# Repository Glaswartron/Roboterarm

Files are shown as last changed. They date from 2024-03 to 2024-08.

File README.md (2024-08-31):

DIY Roboterarm mit 3 Freiheitsgraden und Controller, der Servos und einen Stepper-Motor verwendet und komplett mit Fusion 360 und dem 3D-Drucker konstruiert wurde.

Der gesamte Arm kann am Fuß rotiert werden, hierfür ist ein Stepper-Motor mit einem simplem Getriebe zuständig, der im Fuß verbaut ist.  
Der Arm besteht aus einer unteren Halterung, die den unteren Servo aufnimmt. Dieser bewegt den gesamten Arm.  
Am Arm selber ist ein zweites Gelenk, das heißt ein zweiter Servo, verbaut, der den oberen Teil des Arms bewegt.  
Alle drei Motoren werden von einem Arduino mithilfe eines Joystick-Controllers gesteuert.  

Beim Bau und Test gab es einige Herausforderungen:
- Das größte Problem ist ein mechanisches: Die Servos können den Arm zwar bewegen, allerdings reicht ihr Drehmoment bzw. ihr Getriebe nicht ganz aus, 
um den Arm z.B. im "ausgestreckten" Zustand zu halten. Um dies zu lösen habe ich den Arm etwas verkürzt, 
versucht beim 3D-Druck Gewicht zu sparen und insbesondere Gummibänder mit Halterungen verbaut, die der Gewichtskraft ein zusätzlich Gegendrehmoment entgegensetzen.
Das funktioniert leider noch nicht perfekt, aber gut genug. Eine mögliche Weiterentwicklung wären stärkere Servos.
- Der Stepper-Motor benötigt einen Treiber mit eigener Stromversorgung und Kühlkörper (läuft heiß). Hierfür kann eine 9V-Batterie angeschlossen werden. Als rudimentäre
Spannungsstabilisierung zwischen Batterie und Stepper-Treiber dient ein (Elektrolyt)Kondensator. Eine mögliche Weiterentwicklung wäre eine bessere Spannungsversorgung mit Spannungsregler(n),
die dann auch gleich den Arduino mitspeisen kann.

Bilder aus der Entwicklung:

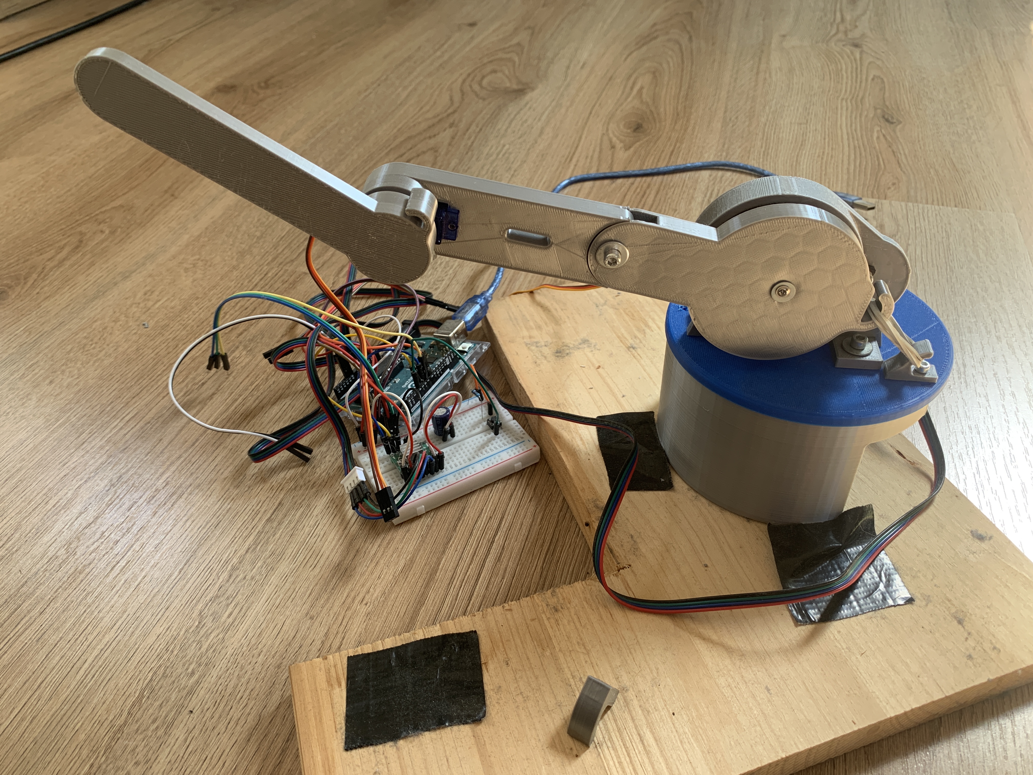
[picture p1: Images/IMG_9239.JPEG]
Vorderansicht

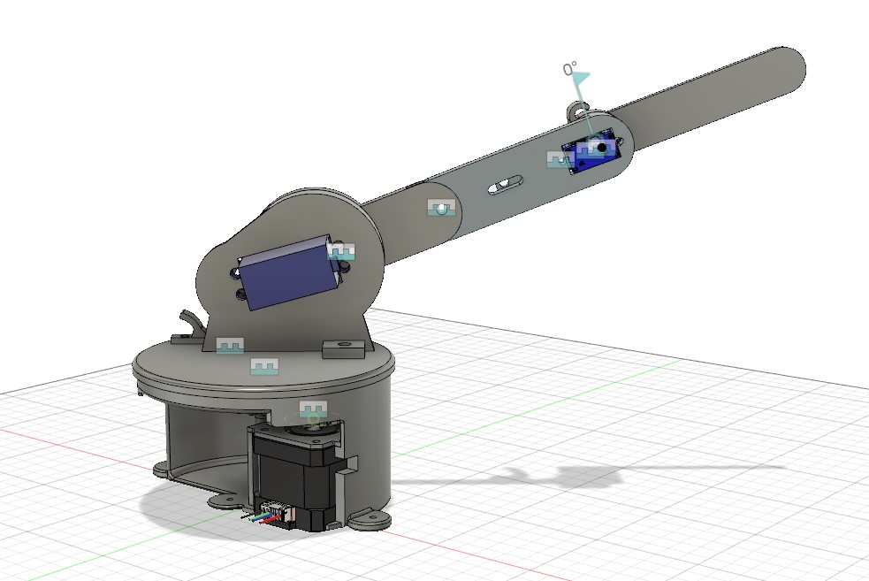
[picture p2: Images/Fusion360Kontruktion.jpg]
Fusion 360 Screenshot

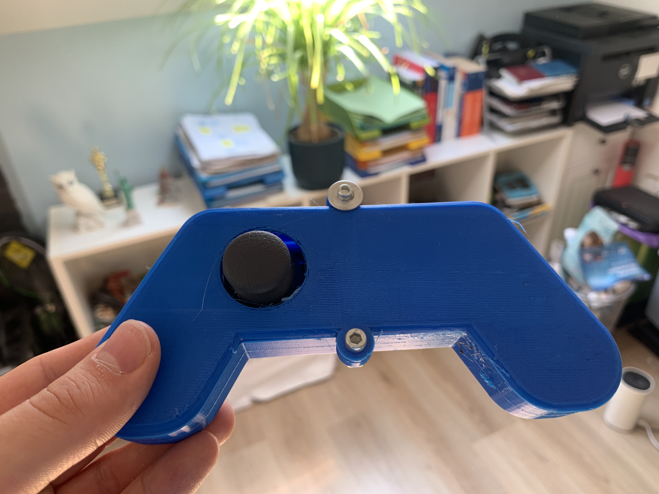
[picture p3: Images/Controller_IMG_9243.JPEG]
Controller

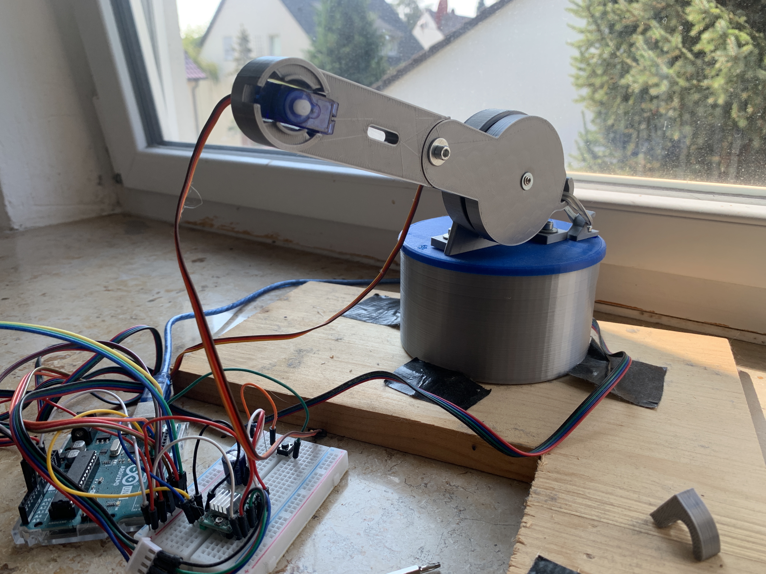
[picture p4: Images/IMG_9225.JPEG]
Vorderansicht Unterarm

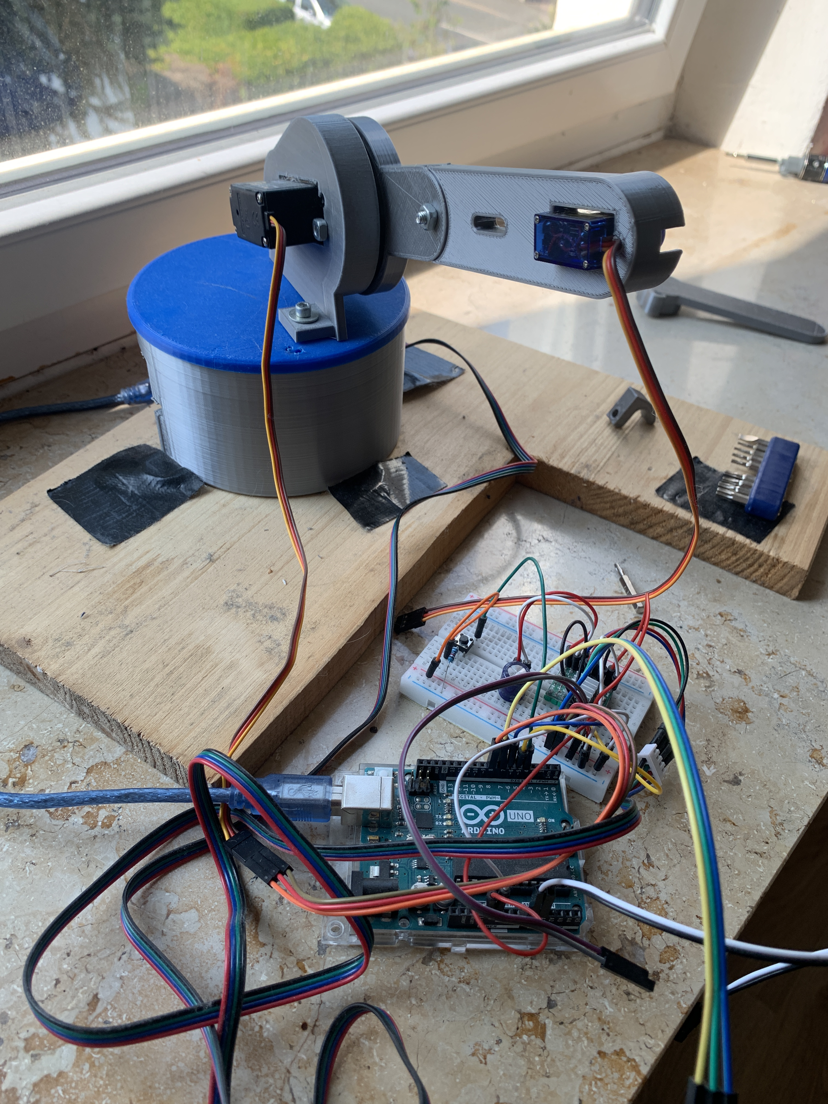
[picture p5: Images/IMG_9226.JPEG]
Vorderansicht Unterarm Seite

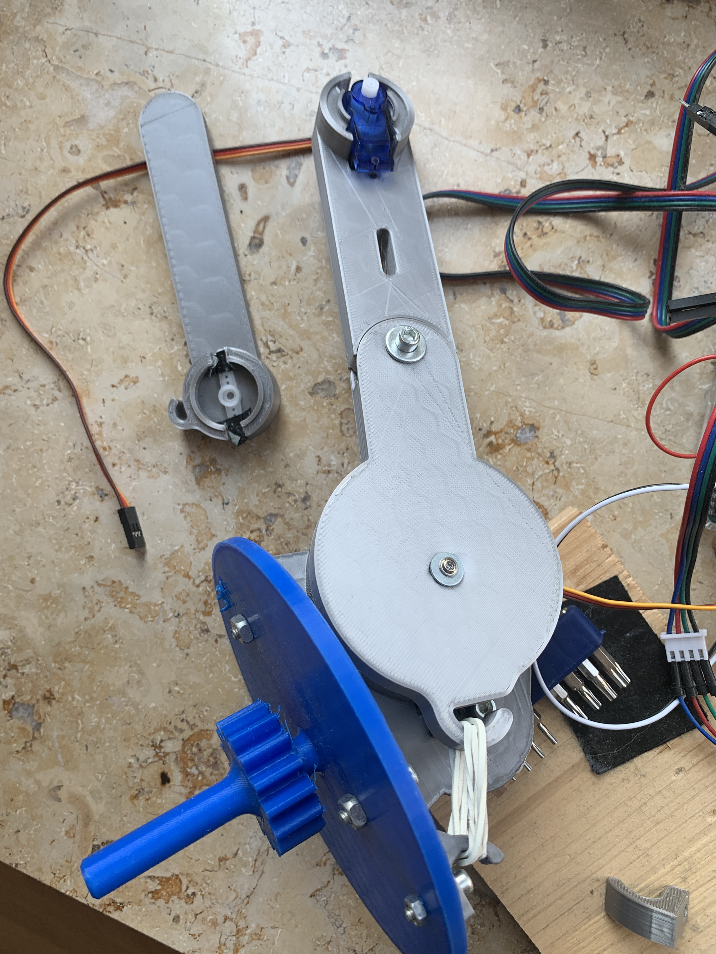
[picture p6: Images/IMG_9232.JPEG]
Einzelteile

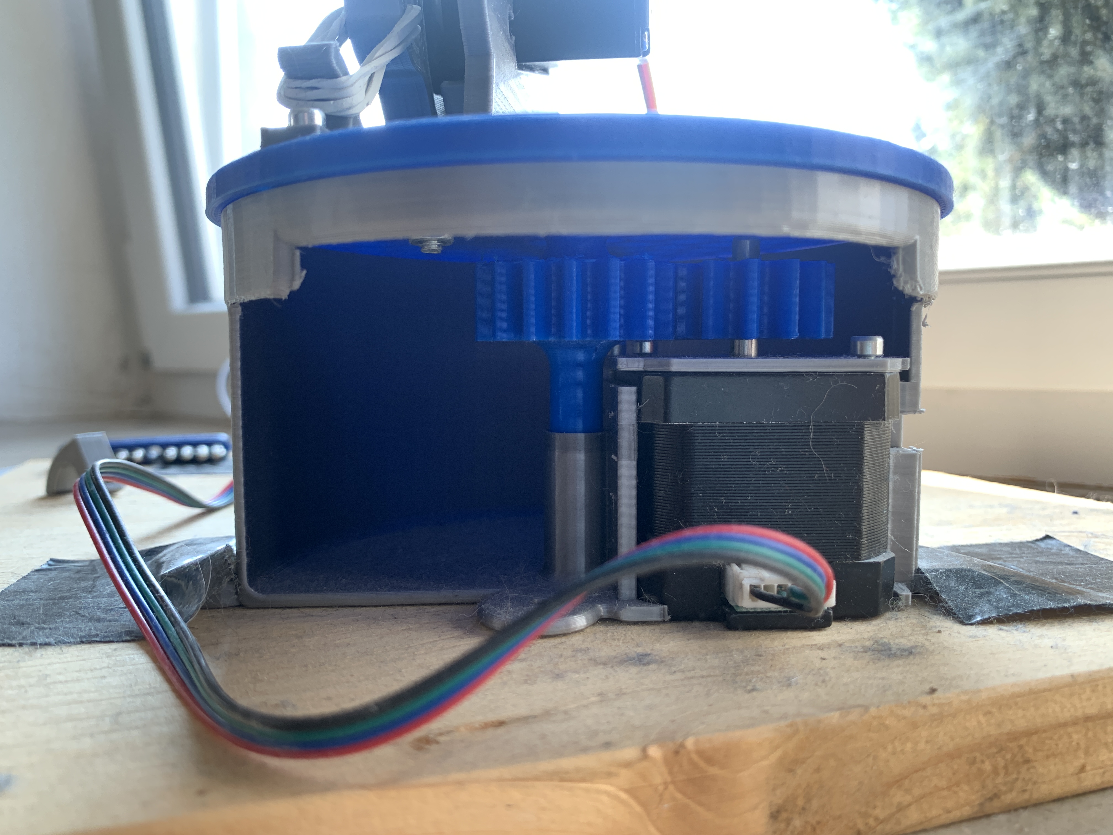
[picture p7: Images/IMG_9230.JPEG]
Fuß mit Stepper und Getriebe

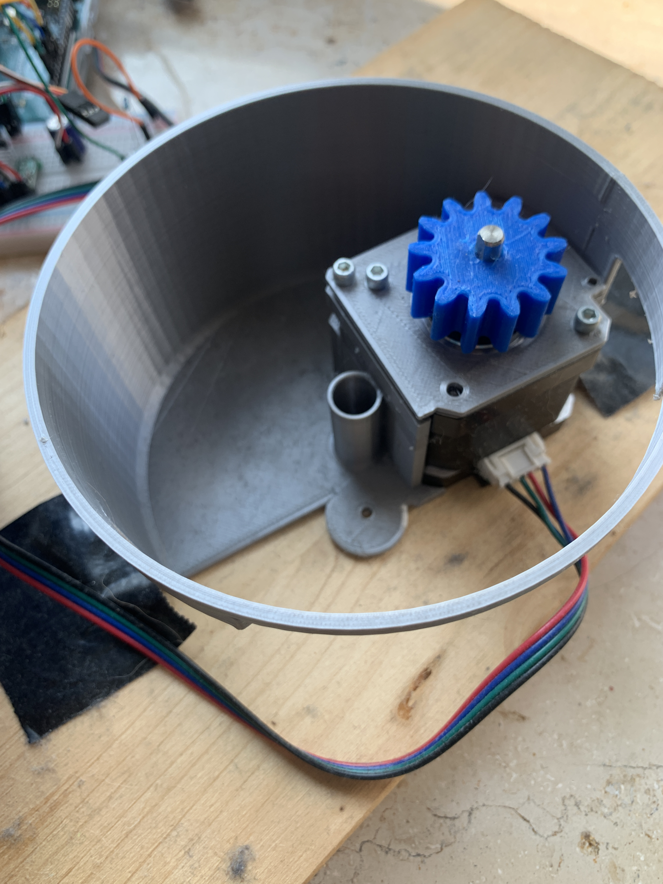
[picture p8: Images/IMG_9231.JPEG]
Fuß mit Stepper offen


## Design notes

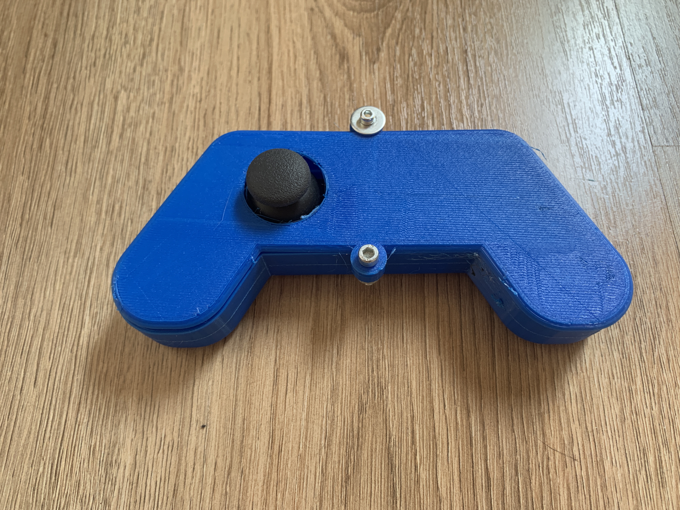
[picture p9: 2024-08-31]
Images/Controller_IMG_9245.JPEG

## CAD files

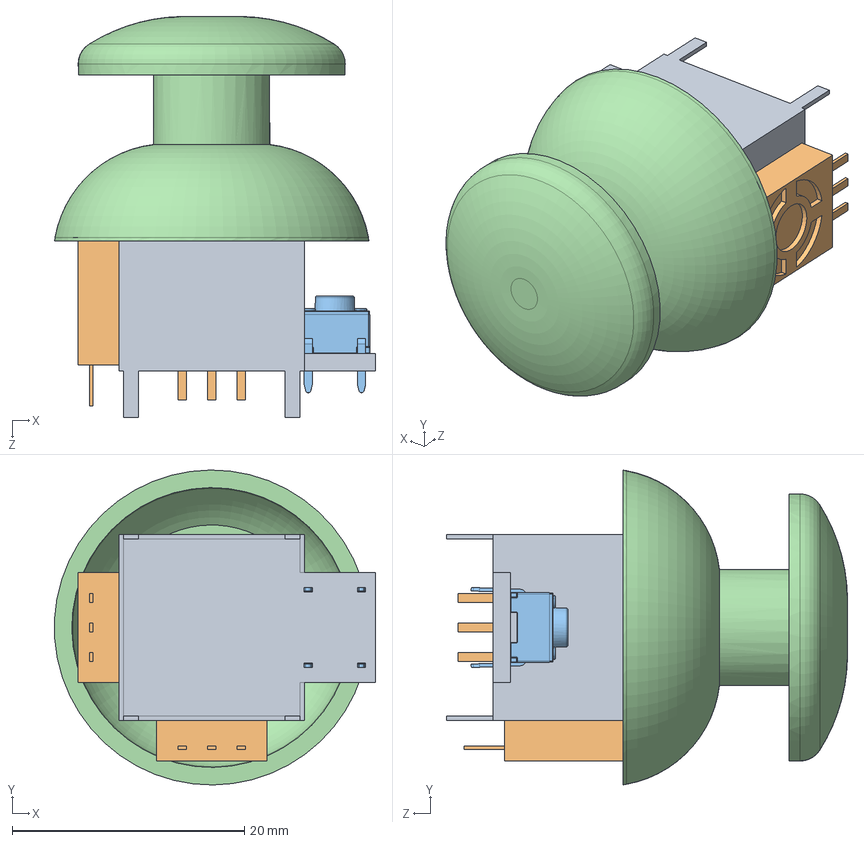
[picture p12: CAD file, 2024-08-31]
3D/dual-axis-xy-joystick-module-with-push-button-1.snapshot.1/Joystick/Thumb Joystick.SLDASM
27.6 x 27.1 x 34.5 mm
potentiometer x 2
tactileswitch-short
joystickhead

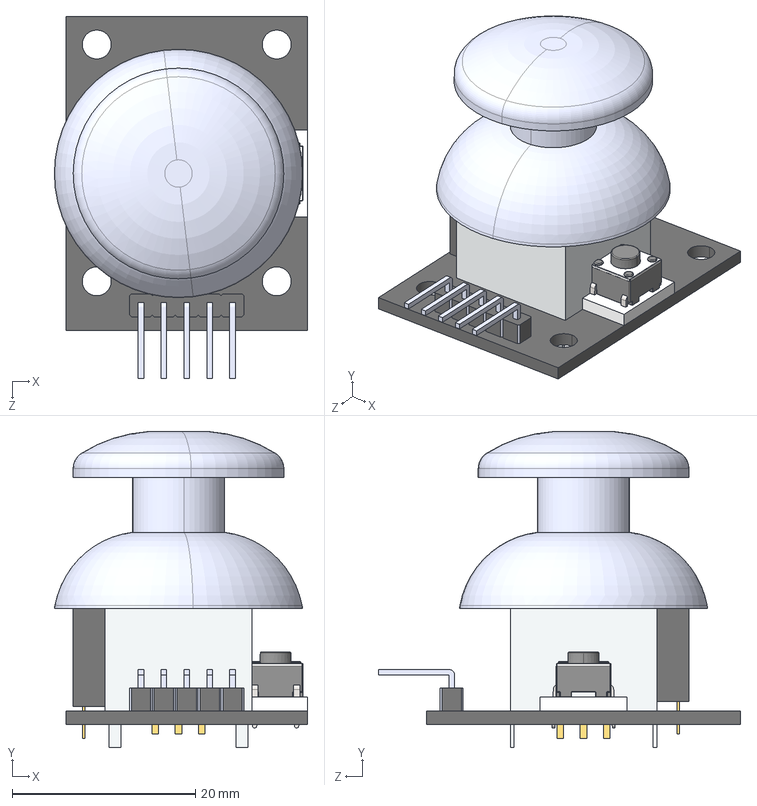
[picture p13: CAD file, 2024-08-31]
3D/dual-axis-xy-joystick-module-with-push-button-1.snapshot.1/Joystick/Joystick assembly.STEP
27.7 x 34.5 x 39.5 mm
board
potentiometer___ x 2
tactileswitch-short
joystickhead___

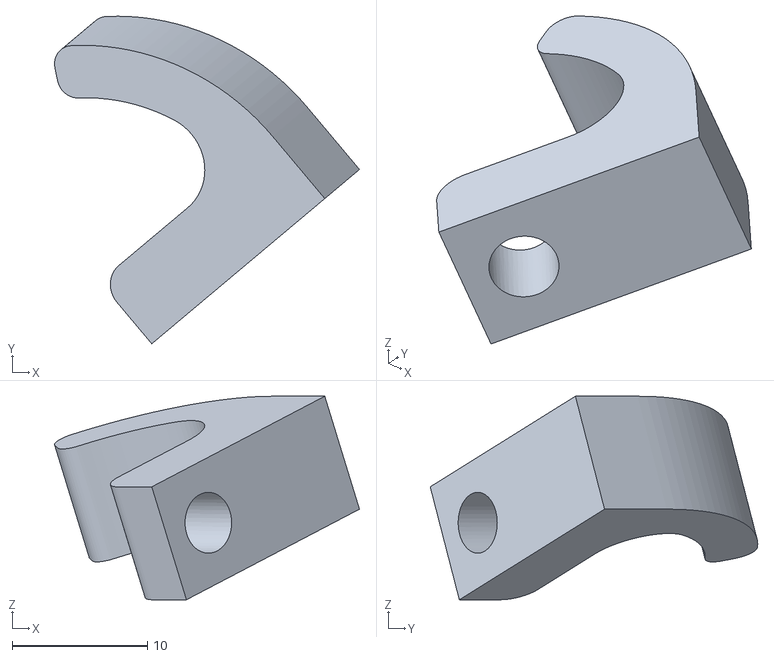
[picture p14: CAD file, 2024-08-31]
3D/GummiHalterOben.stl
22.6 x 24.2 x 15.1

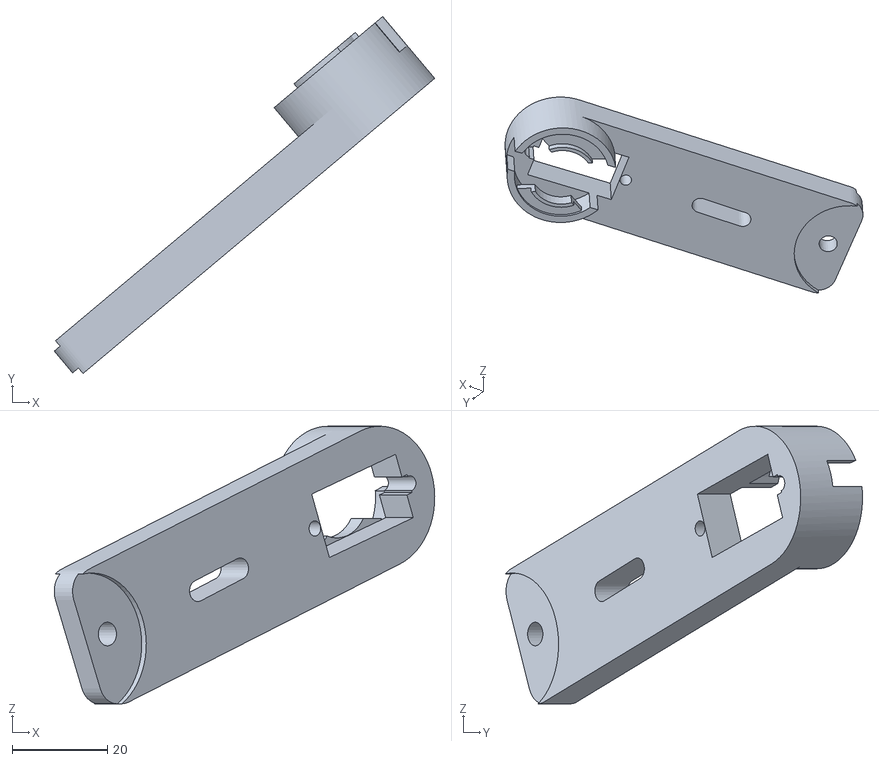
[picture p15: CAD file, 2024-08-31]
3D/ArmOben.stl
80.0 x 75.1 x 58.4

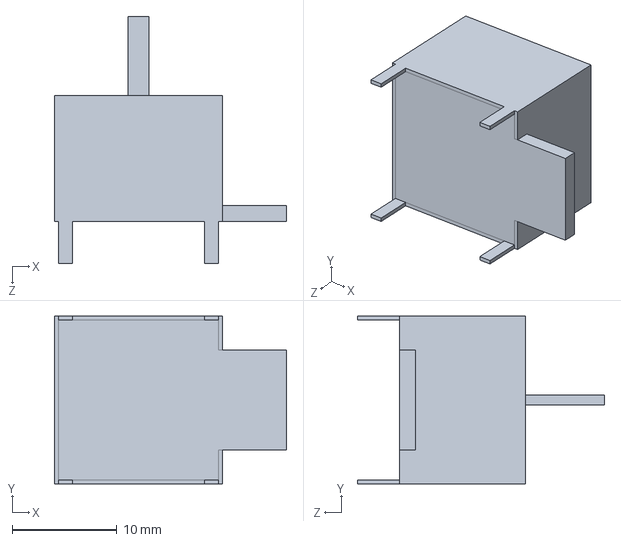
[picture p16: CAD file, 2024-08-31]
3D/dual-axis-xy-joystick-module-with-push-button-1.snapshot.1/Joystick/body.SLDPRT
22.1 x 16.0 x 23.5 mm

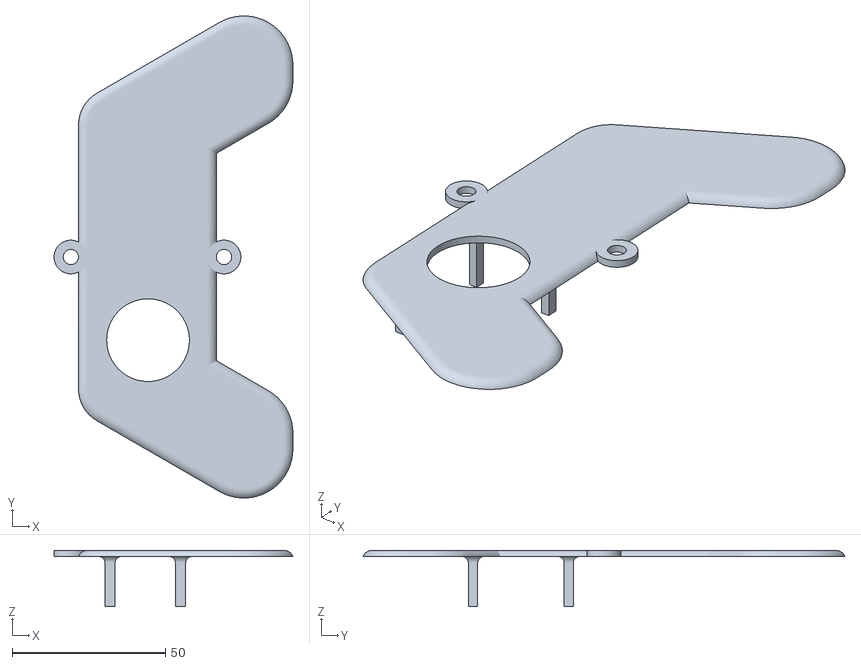
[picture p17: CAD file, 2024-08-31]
3D/DeckelMitJoystickCutout.stl
78.0 x 157.3 x 18.3

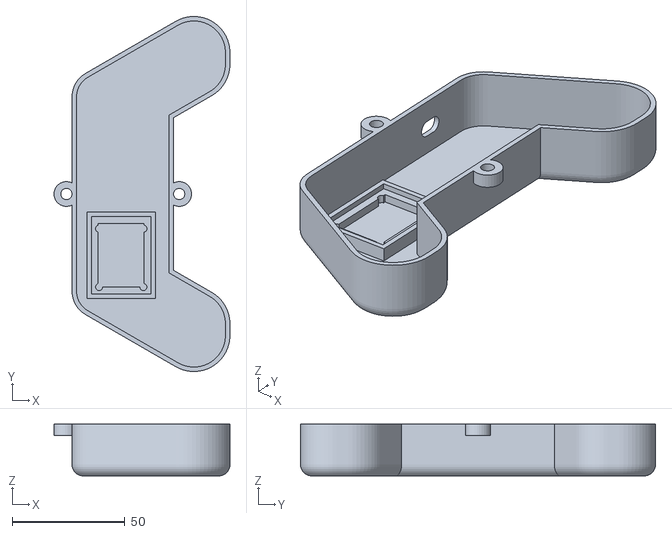
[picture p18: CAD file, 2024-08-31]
3D/ControllerBasisMitJoystickslot.stl
78.0 x 157.3 x 23.0

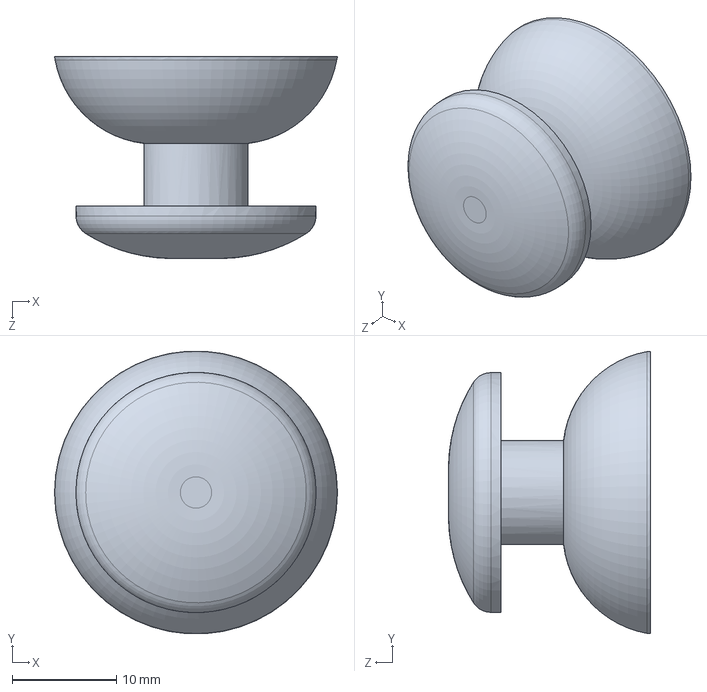
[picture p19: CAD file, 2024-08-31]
3D/dual-axis-xy-joystick-module-with-push-button-1.snapshot.1/Joystick/joystickhead.SLDPRT
27.1 x 27.1 x 19.3 mm

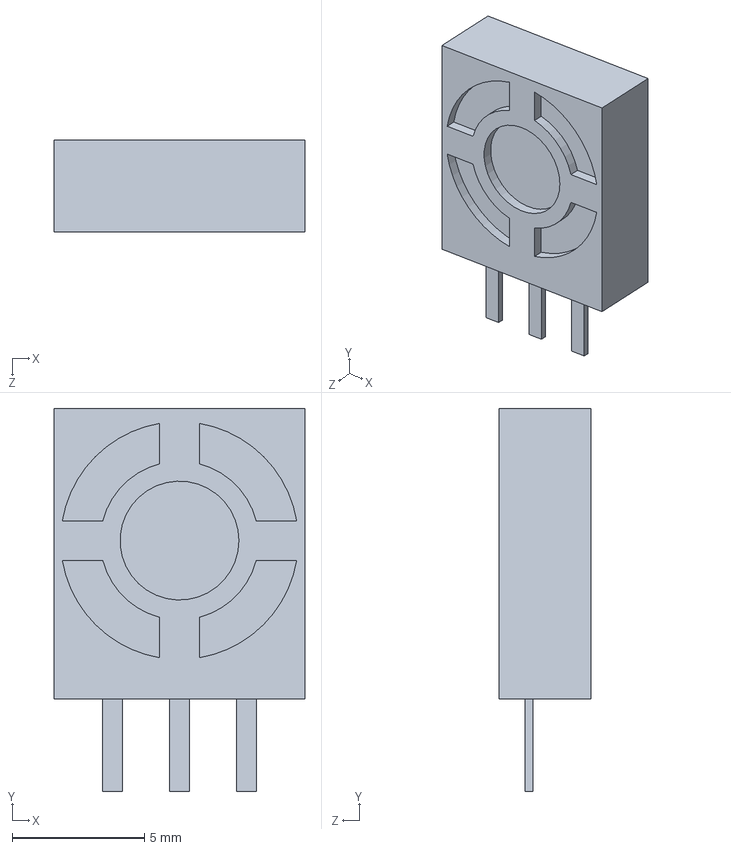
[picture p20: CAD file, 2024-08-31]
3D/dual-axis-xy-joystick-module-with-push-button-1.snapshot.1/Joystick/potentiometer.SLDPRT
9.50 x 14.5 x 3.50 mm

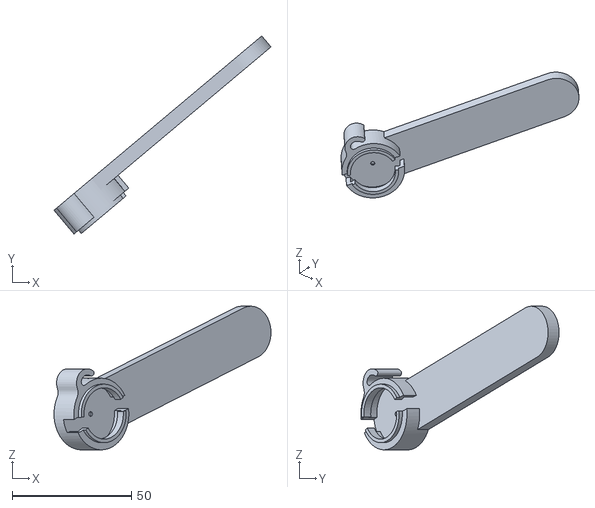
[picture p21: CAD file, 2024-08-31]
3D/ObererArm.stl
90.9 x 83.0 x 60.1

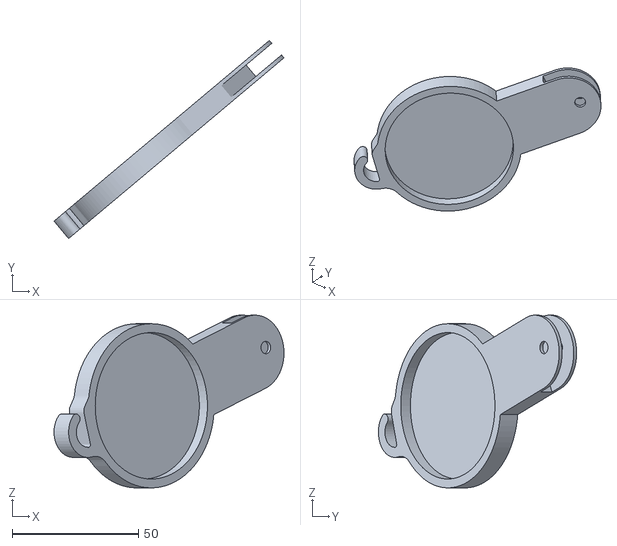
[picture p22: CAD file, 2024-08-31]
3D/ArmHalter.stl
91.1 x 78.4 x 68.4

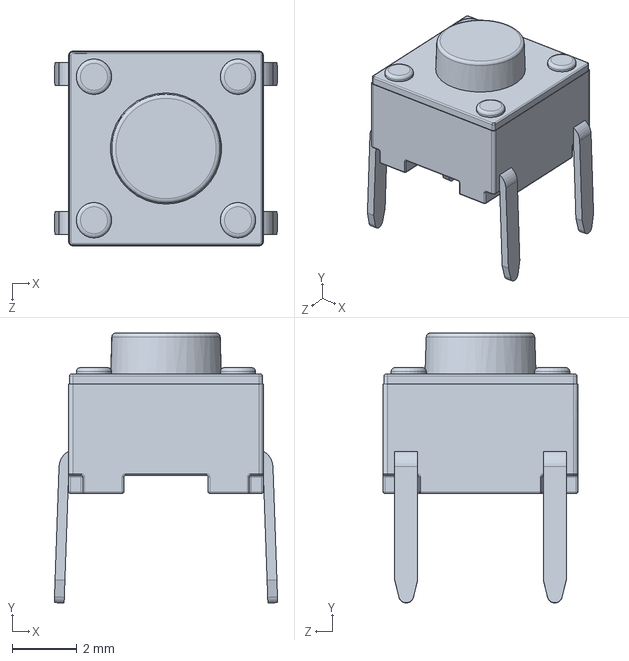
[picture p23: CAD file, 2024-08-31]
3D/dual-axis-xy-joystick-module-with-push-button-1.snapshot.1/Joystick/tactileswitch-short.SLDPRT
6.89 x 8.33 x 6.01 mm

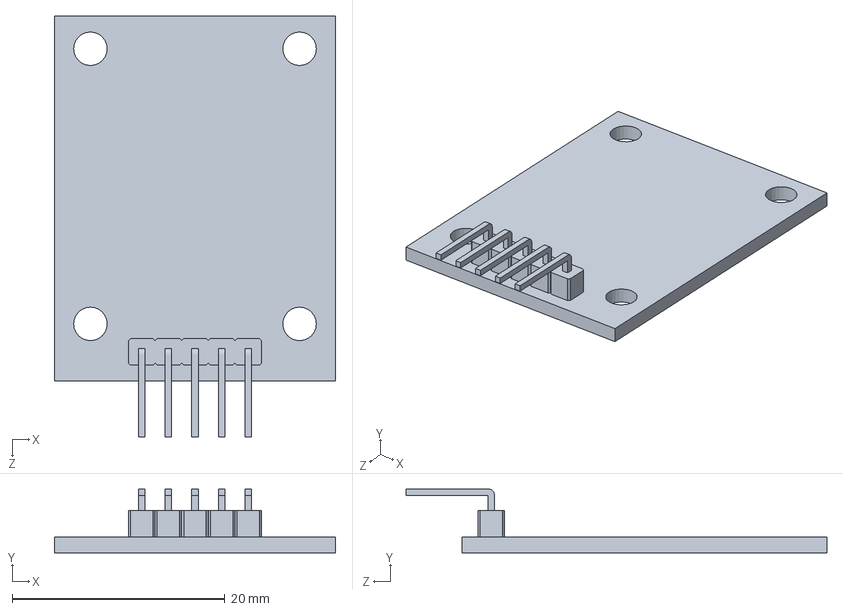
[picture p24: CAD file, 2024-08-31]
3D/dual-axis-xy-joystick-module-with-push-button-1.snapshot.1/Joystick/board.SLDPRT
26.4 x 6.01 x 39.5 mm

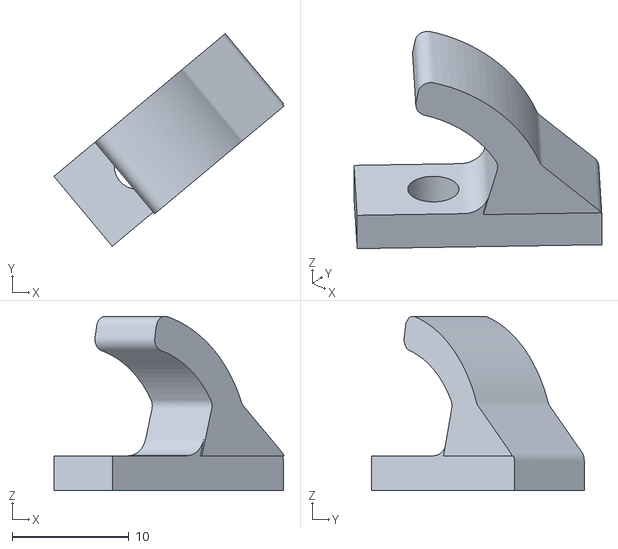
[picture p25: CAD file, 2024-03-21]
3D/Gummi Halterung.stl
19.7 x 18.2 x 15.0

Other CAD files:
3D/GummiHalterungArm.stl
3D/Arm Halterung.stl
3D/Basis.stl
3D/Servo Halterung Test.stl
3D/17HE15-1504S.STEP
3D/Arm Basis Unterer Teil.stl
3D/Arm Basis.stl
3D/ArmBasis.stl
3D/ArmBasisMitZahnrad.stl
3D/ServoHalterung.stl
3D/ServoHalterungTest.stl
3D/Servo_Halterung.stl
3D/Spur Gear (13 teeth).stl
3D/StepperBefestigung.stl
3D/dual-axis-xy-joystick-module-with-push-button-1.snapshot.1/Joystick/Joystick assembly.SLDASM

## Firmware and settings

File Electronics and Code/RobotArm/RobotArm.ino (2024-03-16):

#include <AccelStepper.h>
#include <Servo.h>

#define STEPPER_PIN0 1
#define STEPPER_PIN1 5
#define STEPPER_PIN2 6

#define JOYSTICK_PIN_X A0
#define JOYSTICK_PIN_Y A1

#define ARM_1_SERVO_PIN 8
#define ARM_2_SERVO_PIN 7

#define ARM_SWITCH_BUTTON_PIN 4

AccelStepper stepper(STEPPER_PIN0, STEPPER_PIN1, STEPPER_PIN2);
Servo arm1Servo;
Servo arm2Servo;

float servo1Pos;
float servo2Pos;

float mapFloat(float x, float in_min, float in_max, float out_min, float out_max) {
  return (x - in_min) * (out_max - out_min) / (in_max - in_min) + out_min;
}

void setup() {
  // put your setup code here, to run once:
  arm1Servo.attach(ARM_1_SERVO_PIN);
  arm1Servo.write(180);
  servo1Pos = 180.0;

  arm2Servo.attach(ARM_2_SERVO_PIN);
  arm2Servo.write(120);
  servo2Pos = 120.0;

  stepper.setMaxSpeed(50);

  pinMode(ARM_SWITCH_BUTTON_PIN, INPUT);

  Serial.begin(9600);
}

void loop() {
  //stepper.setSpeed(50);
  //stepper.runSpeed();

  int x = analogRead(JOYSTICK_PIN_X);
  int y = analogRead(JOYSTICK_PIN_Y);

  int xCentered = x - 502;
  int yCentered = y - 513; 

  if (abs(xCentered) >= 100) {
    int xMapped = map(xCentered, -502, 521, -50, 50);

    //Serial.print("x_mapped: "); Serial.print(x_mapped);
    //Serial.print("\n");
    //Serial.print("y_mapped: "); Serial.print(y_mapped);
    //Serial.print("\n");

    stepper.setSpeed(xMapped);
    stepper.runSpeed();
  } else {
    stepper.setSpeed(0);
  }

  if (abs(yCentered) >= 100) {

      float yMapped = mapFloat(yCentered, -513.0, 523.0, -0.05, 0.05);

      int armSwitchButtonState = digitalRead(ARM_SWITCH_BUTTON_PIN);

      if (armSwitchButtonState == LOW) {
        if (servo1Pos + -1 * yMapped <= 180.0 && servo1Pos + -1 * yMapped >= 0.0) {
          servo1Pos += -1 * yMapped;
        }
        arm1Servo.write(servo1Pos);
      } else {
        if (servo2Pos + -1 * yMapped <= 180.0 && servo2Pos + -1 * yMapped >= 0.0) {
          servo2Pos += -1 * yMapped;
        }
        arm2Servo.write(servo2Pos);
      }
  }



  //Serial.print("X: "); Serial.print(x); Serial.print(",  "); Serial.print("Y: "); Serial.print(y);
  //Serial.print("\n");
}

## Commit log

2023-12-03 Neue Servo- und Armhalterung
    [Arm Halterung.stl]
2023-12-03 Unterer Teil vom ersten Arm
    [ArmHalter.stl]
2024-03-16 Code und STL-Dateien für 3D-Druck
    [ArmHalter.stl, ArmOben.stl, Gummi Halterung.stl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]
2024-03-21 Gummi-Halterung überarbeitet
    [Gummi Halterung.stl, GummiHalterungBasis.stl]
2024-03-22 Gummihalterungen Oberer Arm
    [GummiHalterOben.stl, ObererArm.stl]
2024-08-31 Controller und Verbesserungen am oberen Arm
    [ArmHalter.stl, ArmOben.stl, ControllerBasisMitJoystickslot.stl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]
